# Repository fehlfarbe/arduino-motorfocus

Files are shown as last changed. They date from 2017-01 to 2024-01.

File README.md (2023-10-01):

# arduino-motorfocus

Simple moonlite focuser protocol implementation for Arduino and stepper motors.

Tested with Arduino Nano and cheap [28BYJ-48 stepper motor with driver](https://arduino-info.wikispaces.com/SmallSteppers) and [INDI / Ekos](http://indilib.org). Works also with [Pololu A4988 Stepper Motor Driver](https://www.pololu.com/product/1182) (see wiring).

Updated 3D/CAD models for TS 65/420 Quadruplet are available at Thingiverse: <https://www.thingiverse.com/thing:2063325>
Motor focuser for Starlight Feather Touch 2" by Cover1987: <https://www.thingiverse.com/thing:3593910>

## Installation

### Webupload via browser's Web Serial API

Only available for Chrome/Chromium at the moment. Visit <https://fehlfarbe.github.io/arduino-motorfocus>, connect your Arduino Nano and click the right button to upload the latest version :)

### Install via PlatformIO

1. Download and install [PlatformIO](https://platformio.org/install/ide?install=vscode)
2. Clone or download this project and unzip it
3. Open project with PlatformIO
4. Select the right config for your microcontroller e.g. `nanoatmega328` for Arduino Nano with 28BYJ-48 stepper, `promicro16` for Sparkfun Pro Mirco with 28BYJ-48 stepper or `nanoatmega328_A988driver` for Arduino Nano with A4988driver support in the bottom bar and upload to your Arduino (PlatformIO will download needed libraries automatically)

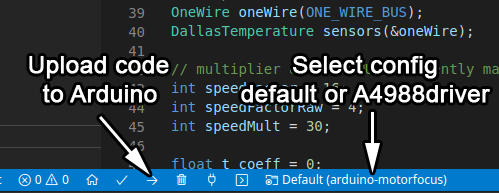
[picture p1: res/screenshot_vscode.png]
VSCode settings


## Wiring

### Wiring for 28BYJ-48 stepper motor with ULN2003A breakout board

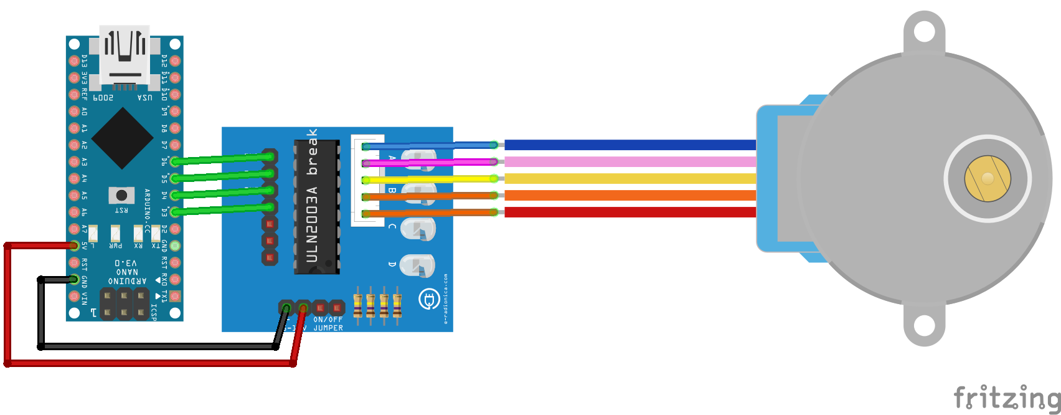
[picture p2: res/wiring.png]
28BYJ-48 wiring


### Wiring for A4988 driver

Select config `A4988driver` in VSCode bottom bar (step 4). You can change the microstep resolution (full step, half step, ...) with MS1, MS2, MS3 pins on the driver board. See more at [Pololu A4988 Stepper Motor Driver doc](https://www.pololu.com/product/1182) (Step (and microstep) size). If all pins are unconnected the driver will run in full step mode.
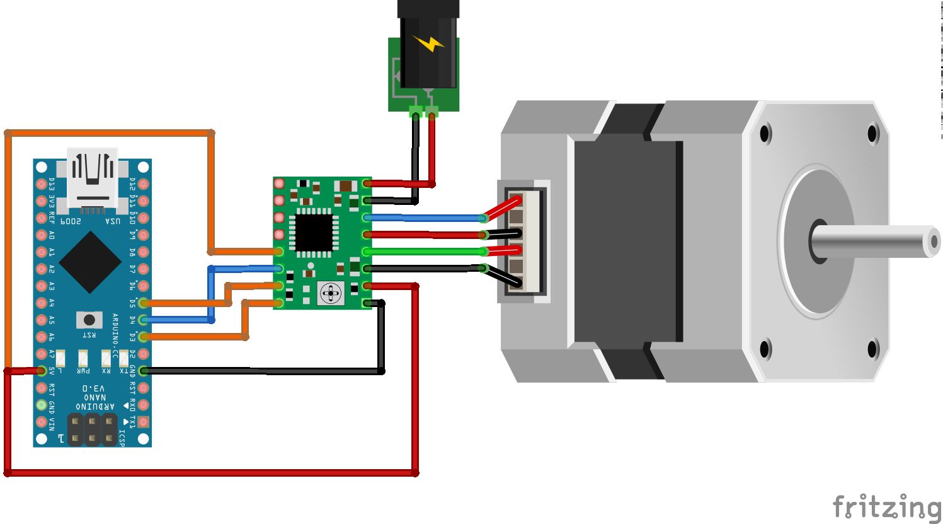
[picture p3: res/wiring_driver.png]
Stepper with driver wiring


### Wiring for in/out buttons

The internal pullups are active so you have to connect your buttons for manual focus to GND. The potentiometer is optional and can limit the maximum speed for manual focus.
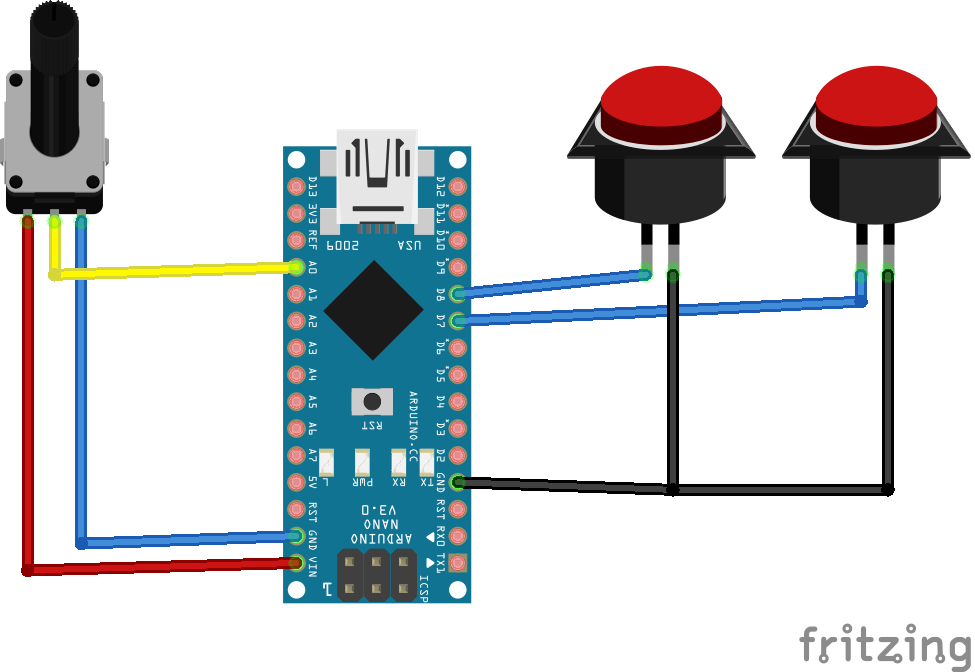
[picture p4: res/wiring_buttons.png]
Buttons wiring


### Wiring for temperature sensor DS18B20

You need a 4.7kΩ pullup resistor. If there is no sensor attached the temperatur will be zero.
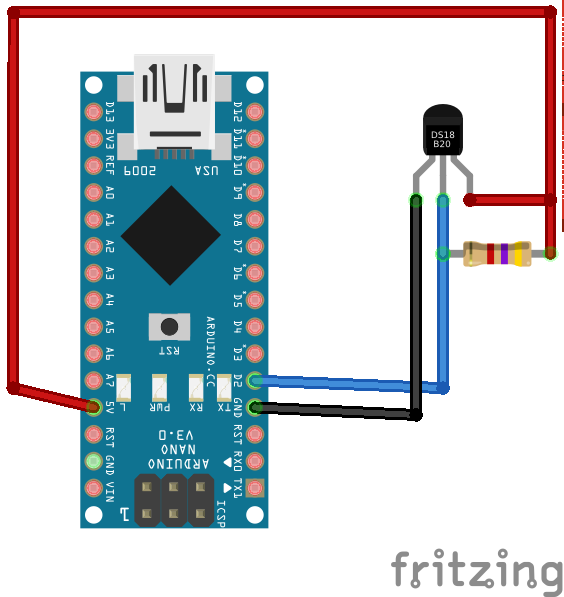
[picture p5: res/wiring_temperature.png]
DS18B20 wiring


## Troubleshooting

### ASCOM driver cant find the focuser

Some people reported problems with arduino-motorfocus and Windows/ASCOM. If you use the ASCOM-Moonlite.DRO.Focuser driver the focuser doesn't appear in the setup list.

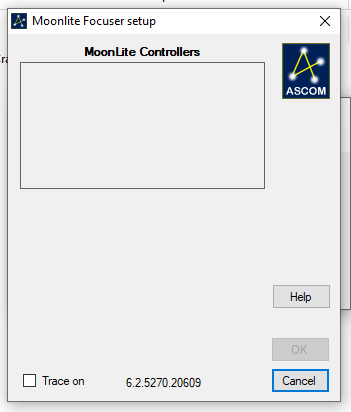
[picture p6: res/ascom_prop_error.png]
ASCOM driver cannot find focuser


This happens because the setup opens all COM ports, sends a command and waits for a proper response. Unfortunally Windows resets the device when the port is opened (DTR is set to low) and an Arduino clone needs a second or so to boot up so it won't receive the command and the setup gets a timeout. There are multiple ways to solve the problem:

1. You can flash the [MiniCore Bootloader](https://github.com/MCUdude/MiniCore) to your Arduino. This bootloader is faster and in my tests it was fast enough to get detected by the setup

2. Just install a 10µF or 33µF between RST and GND or remove the 100nF capacitor on the bottom of your Nano. You can see an image of the capacitor and further explanation on [this website](https://www.astroscopic.com/blog/disable-arduinos-auto-reset-connection)

3. Use a different Microcontroller like Arduino Pro Mini with an external USB-TTL converter and dont't connect the DTR line

And voilà the focuser will show up:

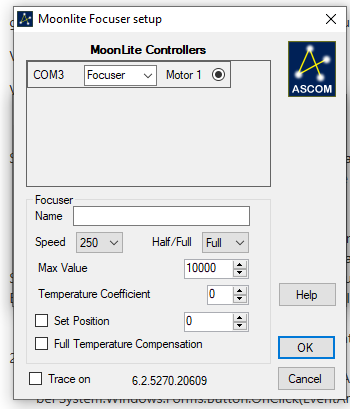
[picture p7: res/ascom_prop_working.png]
ASCOM setup finds focuser


### ASCOM driver finds the focuser but can't connect

Same problem as above. Unfortunally the first solution, flashing the bootloader, didn't work for me but the additional capacitor between RST and GND works.

### Other ASCOM errors

If there are different errors, please [open an issue](https://github.com/fehlfarbe/arduino-motorfocus/issues) and attach the logfile. You can activate logging for you focuser in the properties setup:

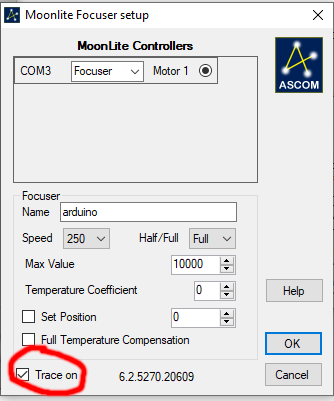
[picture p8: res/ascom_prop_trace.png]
ASCOM setup finds focuser


The logfile is located in `%HOMEPATH%\Documents\ASCOM`

You can also connect an USB-TTL converter to GPIO 10 to see all commands sent by your computer and some debug messages.

### The motor moves very slow

* Don't use a DEBUG build because SoftwareSerial printing slows down the microcontroller
* Check the full/half/... microstep setup of your driver
* Increase SPEED_MULTIPLICATOR and ACCELERATION in arduino-motorfocus.h

### The motor doesn't move

* Check wiring between microcontroller and your driver
* Check if manual focusing via buttons is working
* Check wiring between motor and driver, sometimes the motor coil cables are mixed up

## PCB

I made a simple PCB that connects all the parts and supports Pololu style driver boards and ULN2003A breakout board. The KiCAD project and gerber files are located at `hardware`.
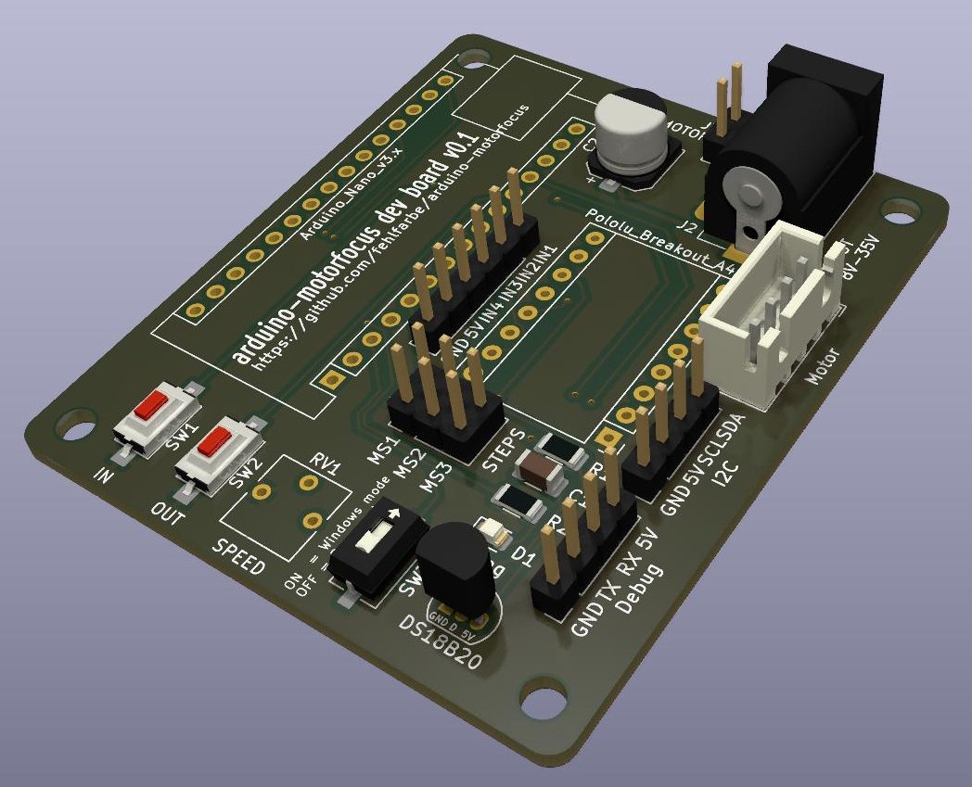
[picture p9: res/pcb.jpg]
PCB

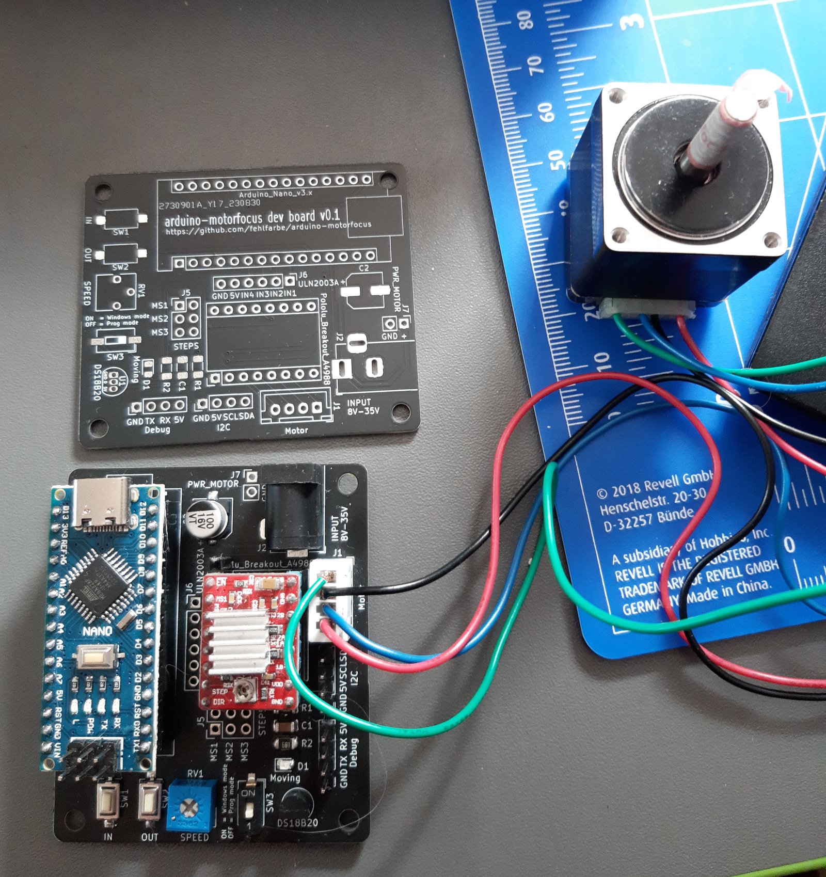
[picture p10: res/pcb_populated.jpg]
Populated PCB


## Arduino-motorfocus mounted on TS65/420 Quadruplet

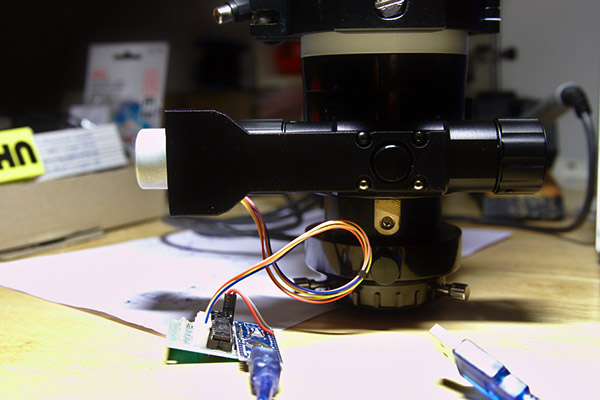
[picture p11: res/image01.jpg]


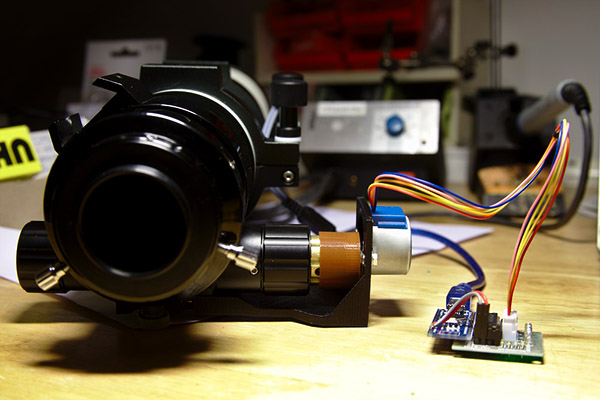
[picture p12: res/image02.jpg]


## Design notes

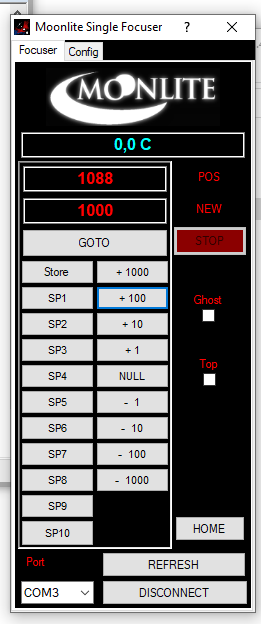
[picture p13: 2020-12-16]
res/standalone.png

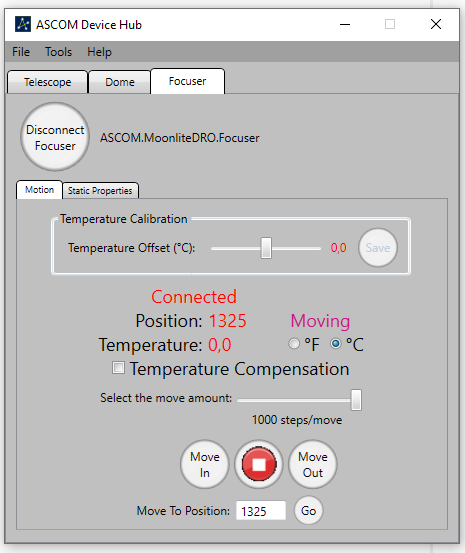
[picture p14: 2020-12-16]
res/ascom_working.png

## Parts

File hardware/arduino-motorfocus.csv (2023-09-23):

Source: | /home/kolbe/Arduino/arduino-motorfocus/hardware/arduino-motorfocus/arduino-motorfocus.kicad_sch
Date: | Sat 23 Sep 2023 21:14:49 CEST
Tool: | Eeschema 7.0.7-7.0.7~ubuntu22.04.1
Generator: | /usr/share/kicad/plugins/bom_csv_grouped_by_value.py
Component Count: | 23
Collated Components:
Item | Qty | Reference(s) | Value | LibPart | Footprint | Datasheet | DNP
1 | 1 | A1 | Arduino_Nano_v3.x | MCU_Module:Arduino_Nano_v3.x | Module:Arduino_Nano | http://www.mouser.com/pdfdocs/Gravitech_Arduino_Nano3_0.pdf
2 | 1 | A2 | Pololu_Breakout_A4988 | Driver_Motor:Pololu_Breakout_A4988 | Module:Pololu_Breakout-16_15.2x20.3mm | https://www.pololu.com/product/2980/pictures
3 | 1 | C1 | 10uF | Device:C | Capacitor_SMD:C_1206_3216Metric | ~
4 | 1 | C2 | 100uF | Device:C_Polarized | Capacitor_SMD:CP_Elec_6.3x5.9 | ~
5 | 1 | D1 | Moving | Device:LED | LED_SMD:LED_0805_2012Metric | ~
6 | 4 | H1, H2, H3, H4 | MountingHole | Mechanical:MountingHole | MountingHole:MountingHole_3.2mm_M3 | ~
7 | 1 | J1 | Motor | Connector:Conn_01x04_Pin | Connector_JST:JST_XH_B4B-XH-A_1x04_P2.50mm_Vertical | ~
8 | 1 | J2 | PWR_MOTOR | Connector:Barrel_Jack_Switch | Connector_BarrelJack:BarrelJack_Horizontal | https://de.aliexpress.com/item/1005002561919358.html
9 | 1 | J3 | Debug | Connector:Conn_01x04_Pin | Connector_PinHeader_2.54mm:PinHeader_1x04_P2.54mm_Vertical | ~
10 | 1 | J4 | I2C | Connector:Conn_01x04_Pin | Connector_PinHeader_2.54mm:PinHeader_1x04_P2.54mm_Vertical | ~
11 | 1 | J5 | STEPS | Connector_Generic:Conn_02x03_Odd_Even | Connector_PinHeader_2.54mm:PinHeader_2x03_P2.54mm_Vertical | ~
12 | 1 | J6 | ULN2003A | Connector:Conn_01x06_Pin | Connector_PinHeader_2.54mm:PinHeader_1x06_P2.54mm_Vertical | ~
13 | 1 | J7 | PWR_MOTOR | Connector:Conn_01x02_Pin | Connector_PinHeader_2.54mm:PinHeader_1x02_P2.54mm_Vertical | ~
14 | 1 | R1 | 10K | Device:R | Resistor_SMD:R_1206_3216Metric | ~
15 | 1 | R2 | 680 | Device:R | Resistor_SMD:R_1206_3216Metric | ~
16 | 1 | RV1 | SPEED | Device:R_Potentiometer | Potentiometer_THT:Potentiometer_Vishay_T73YP_Vertical | https://de.aliexpress.com/item/1005003399827077.html
17 | 1 | SW1 | IN | Switch:SW_Push | Button_Switch_SMD:SW_SPST_CK_RS282G05A3 | ~
18 | 1 | SW2 | OUT | Switch:SW_Push | Button_Switch_SMD:SW_SPST_CK_RS282G05A3 | ~
19 | 1 | SW3 | WIN | Switch:SW_DIP_x01 | Button_Switch_SMD:SW_DIP_SPSTx01_Slide_6.7x4.1mm_W6.73mm_P2.54mm_LowProfile_JPin | ~
20 | 1 | U1 | DS18B20 | Sensor_Temperature:DS18B20 | Package_TO_SOT_THT:TO-92_Inline | http://datasheets.maximintegrated.com/en/ds/DS18B20.pdf

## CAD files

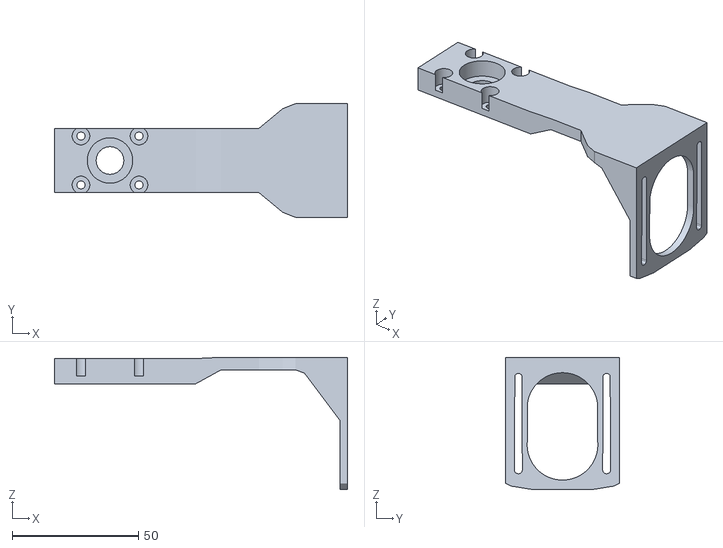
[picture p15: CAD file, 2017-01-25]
res/oaz_focuser_quadruplet_v3_04.STL
116.2 x 45.0 x 52.5

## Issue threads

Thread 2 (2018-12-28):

Buttons not worked for me, here is my solution.

franky384, 2018-12-28:
First of all, thank you for sharing your code,
but the push buttons never worked for me. So after some days of searching and trial and error i finally found a working solution.
Maybe you can have a look at it ?

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

[sketch_dec28a.html.pdf](https://github.com/fehlfarbe/arduino-motorfocus/files/2715402/sketch_dec28a.html.pdf)

franky384, 2018-12-28:
I have tried it like in that example, but it hadn't worked for me. I can try it again with my changed code.

fehlfarbe, 2019-02-17:
Should be fixed now. I activated the pullup resistors for button input and checked for BUTTON == LOW. So the wiring in your first post is correct.

Closed 2020-12-21.

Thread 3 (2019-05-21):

AccelStepper.h: No such file or directory

AndiPhotonen, 2019-05-21:
Hi,
First of all I'd like to thank you for realizing this nice project.
I downloaded the Project as a zip and extracted it to my Arduino folder.
But when I try to compile it, I get the error that it can't find the AccelStepper.h
Did I miss something or do you have a tip for me?
Thanks!

fehlfarbe, 2019-05-21:
Hey Andi,
the Accellstepper library is missing. You can install the library with Arduino Studios library manager: https://www.arduino.cc/en/Guide/Libraries just search for accelstepper, install the current version and recompile.

AndiPhotonen, 2019-05-22:
Thank you! now it works fine

Closed 2019-05-22.

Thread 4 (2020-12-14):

Not anymore compatible to Moonlight SW

energiebrand, 2020-12-14:
Hi,
Build the controller using an Arduino NANO clone (FTDI chip), ULN2003 stepper druver and the gear stepper motor. The sketch works out of the box when using the manual control via the buttons.

Just for fun I tried to use the original Moonlight non-ASCOM controller SW but unfortunately it only connects, read the temperature and actual step value and does nothing. The Moonlight SW hangs up (WIN 10 and WIN7). When connecting via PUTTY serial, everything works fine. All listed commands are working.

Then tried the Moonlight ASCOM driver. The driver is recognized by CCDCiel SW for example. Then I open an ALPACA driver and this opened the Moonlight ASCOM driver. But this ASCOM driver does not recognize the Adrduino (sketch).

So I think maybe Moonlight changed something in their SW (Non-ASCOM controller App as well as Ascom driver) so that your sketch is non more supported. Could that be? Did you try to to connect with the latest Moonlight SW?
Best regards and however thanks for the Sketch!

fehlfarbe, 2020-12-14:
Hi,

to be honest I tested the setup only with the INDI moonlite driver. But many people asked in the last weeks if it will run on Windows with ASCOM. So I set up a Win10 VM and tested the "Moonlite Single Focuser" which worked like expected (just with my nano and the motor on a breadboard)

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

Then I tried the Moonlite DRO ASCOM driver but it can't even find the COM port:
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
Seems like the driver opens all COM ports, sends a command and waits for the right response. Unfortunately the Arduino Nano resets when the COM port is opened and it takes 200ms or so before it's ready to receive commands which takes too long for the Moonlite driver.
You can turn off the auto reset with a 10nF capacitor between RST and GND (I tried a 47nF which is also working).
Then open the properties windows again and the Arduino will show up. If not, close the windows, press the RESET button on the Nano and try again. It worked on the second try with my setup.
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

Let me know if it's working, so I can update the readme :smiley:

energiebrand, 2020-12-15:
Hi and thanks a lot for fast response!

The solution with capacitor / Reset seems to be the right way but I have only partly success.
Firstly after connecting a 33nF C the Arduino connects with the Dual Focuser Moonlight SW and I was able to control the motor as expected. Very good!

Then I connected via ASCOM using the Moonlight focuser driver and CCDCiel SW. Now it found the Arduino as a Focuser. Very good!

Then I checked with the Single Focuser Moonlight SW on a WIn7 PC but no success...

Then went back to the WIN10 PC and tried again with the Dual Focuser Moonlight SW...no success anymore!!! I tried with several C´s (15nF, 33nF, 22nF, 1mF, new boot of the PC, Reset manually of the Arduino, no chance anymore. The Arduino always connects in the first or second attempt, send some data (Pos and temperature) and then disconnects. Tried it dozend of times.

After that back to the ASCOM driver and always success. I removed the USB, no focuser, reconnceted the USB and success with the ASCOM driver.

So no luck anymore with the non-ASCOM driver. (I cannot use the Single driver because I deleted the SW in a not correct way and it seems that somewhere parts are remaining. This results in that I cannot anymore install the single focus driver...)

To summerize:
- with Moonlight ASCOM driver working on a WIN10 installation using a 15nF, 33nF, 22nF, 1microF
- unfortunately I cannot do more things with CCDCiel because I do not have a camera, but I can see that there is a communication between the Arduino and the PC (RX and TX LED flashing)
- no permanent connection anymore with Dual focuser SW, just a short data exchange
- also it is not possible to open the ASCOm device hub, but maybe I am doing wrong or anything more is needed

So what to do? Since currently I am only using the "Manual button" function I can live with that.
Also later on when I will go to astrophotographie the ASCOM driver works.
Only limitation for me is the non-Ascom SW.

However the capacitor is working and helps. The other problems seems to be a problem of the used PC and the Arduino clone version.

So no problem with your sketch and I think you should close this issue but add some information. I would recommend to add the C in the description and schematic!

Thanks a lot and if you have any further idea you are welcome!

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

energiebrand, 2020-12-15:
Tried the whole day to get more about the problems I have...

Maybe a 1microF is a better solution. I noticed that the ASCOM driver always recognized the Arduino when the USB cable was connected (...and did not recognize when USB was open), but in many cases there was no communication between the Arduino and the ASCOM driver after the connection was established. So I changed to a 1microF C and RX/TX is flashing constantly.
So that means even if the ASCOM driver windows shows that is has found a COM port and a focuser is detected there could be that there is no communication.

In addition meanwhile I got the Single Focuser Moonlight SW running again but same problem as I had without the C. It connects now stable, sends some information (Temp and Pos.) and after that it freezes...

fehlfarbe, 2020-12-17:
Sorry my bad, I used a 47**µ**F capacitor. I also found different hints/solutions:
- Update the bootloader: the Arduino clones from China have the old bootloader that takes 1-2s too boot up. I flashed the newer Optiboot with [MiniCore](https://github.com/MCUdude/MiniCore) that boots much faster. At least the setup finds the focuser without the capacitor. But I still can't connect with ASCOM Device Hub.
- Remove the 100nF capacitor on the bottom as described here: https://www.astroscopic.com/blog/disable-arduinos-auto-reset-connection. After that you have manually press the reset button if you want to upload a new firmware
- Does it also freeze if you don't connect the temperature sensor? I just wired the motor but no sensor. Maybe the Arduino sends some bad numbers and the driver freezes?
- Sometimes I have to press the "connect" button twice on the SingleFocuser but after that it is stable
- The DualFocuser looses the connection after some seconds. I assume that happens because it sends an unknown command (starting with a number), doesn't get a proper answer and runs into a timeout:
  ```
  [01:01:21:086] Got new command: GT␍␊
  [01:01:21:108] GT:␍␊
  [01:01:21:114] GT␍␊
  [01:01:21:213] temperature: -127.00␍␊
  [01:01:21:267] Got new command: GP␍␊
  [01:01:21:290] GP:␍␊
  [01:01:21:296] GP␍␊
  [01:01:21:301] current motor position: 0x0820 = 2080␍␊
  [01:01:21:345] Got new command: 2GP␍␊
  [01:01:21:365] 2G:P␍␊
  [01:01:21:372] 2GP␍␊
  ```
  I just updated the code so it will ignore the leading "2" and just parses the command. So motor1 and motor2 show the same values. After that the DualFocsuer doesnt disconnect but freezes :laughing: but SingleFocuser still runs fine.

energiebrand, 2020-12-17:
Thanks  a lot for the deep-dive into the problem!
Yes I have seen in an other discussion that someone has used a much bigger C and thats why I tested also with 22 and 47microF. However a 1microF does also the job and connects stable to the Single Manual Focuser SW.

And yes my NANO clone have the old bootloader.

I do not use the temperature sensor, so the pin is open in all my tries. It shows 0° but still freezes with the Single Manual Focuser SW after a first and short data transfer. It changes the display from "No data" to "0" and the temperature to 0°.
I had only one attempt 3 days ago where it works and it was possible to control the motor 100% and I think this was by random.

Using the Dual Focuser SW: the Arduino connects also, shows the 0 values on both rows but than disconnects after 5 seconds like yours, but without your sketch modification!

Now the bad thing for you... :-(  yesterday I completed my installation and closed the cover. As I said currently I will use the focuser just manually with the buttons in a hand-box I am printing at this moment.
So with this installation I will not going on to flash a new bootloader. However it would be very interesting to continue and see the results. Unfortunately at the moment I don't have another NANO for more testing.

But it could be that when changing to astrophotography I will use your solution again and need a SW a (ASCOM) controlled focuser. Then I will come back to your proposals.

But regarding the ASCOM driver. Like you my NANO will not really run with it. It connects and most time I see a continously data transfer (RX/TX LED flashing) but no chance to control the motor. Maybe it is the missing astro camera maybe it will not work anyway.

So from my side I will stop here with the current installation but will answer here if I got new results with another NANO I will buy in the future. Thanks a lot for your works! Well I think think discussion will help other people if they are running into similar problems. Attached some pictures of my Newton and the focuser. :-)

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

fehlfarbe, 2020-12-21:
Nice prints! I added your Thingiverse CAD models to the readme :smiley:

If you want to do further investigations you can enable trace/logging in ASCOM and maybe find an error in the logfile and connect a serial/ttl converter to GPIO 10 and see your Nano's debug output (https://github.com/fehlfarbe/arduino-motorfocus#other-ascom-errors)

I will close the issue for now but feel free to reopen :)

Closed 2020-12-21.

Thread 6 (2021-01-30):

may be a bug...

sergio49, 2021-01-30:
Hi, I think you have a mistake in your hexStrToLong converter preventing speed change to work.

at line 329 I think it should be  :
line.toCharArray(buf, line.length()+1);    (+1 missing)

if you change this you have to delete *16 on current and target positions. Then speed change and positionning works fine in ekos.
I've just tested it.
Thanks for your work I use it on my 80ED too :)

fehlfarbe, 2021-02-02:
Thanks for bugfixing and testing :)
I merged your changes to master

energiebrand, 2021-02-08:
Hi all
thanks for BugFixing!
Used the focuser only manually with a modified sketch (added a switch for fast movement) so far.
Now I´m running the focuser with ASTROBERRY: KStars / EKOS / INDI with the latest modifications and can confirm that it is working!

Closed 2021-12-01.

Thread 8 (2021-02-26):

Motor does not run in script

19dexter86, 2021-02-26:
Hi, the motor turns with the buttons without any problems.
But it does not work via the Moonlight. Temperature is displayed. here is an snippet from the logfile.

[ASCOM.MoonLite.1733.440170 - Kopie.zip](https://github.com/fehlfarbe/arduino-motorfocus/files/6051056/ASCOM.MoonLite.1733.440170.-.Kopie.zip)

19dexter86, 2021-02-26:
problem solved. had to move ist one time with buttons, then it works with sgp

Closed 2021-02-26.

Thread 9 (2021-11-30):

DS18B20 wrong wiring

energiebrand, 2021-11-30:
Hi Marcus,
build your motor-focusser last year and still in operation with Astroberry / INDI on my Newton. We had some discussion about the problem with ASCOM...
Now I developed some new 3D parts for a SVBony APO since the buttons on the 1:10 gear are bigger than yours.
However first time I added an 18B20 and burned my fingers... the wiring on your diagram is wrong. + and - are inverted.

fehlfarbe, 2021-12-01:
You are right! I think the DS18B20 part in Fritzing is wrong because it says VDD | DATA | GND:

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

But data sheet says it's GND | DATA | VDD https://datasheets.maximintegrated.com/en/ds/DS18B20.pdf

The broken Fritzing part might be the reason why I burned my fingers several times on the temperature sensor too :laughing:

Closed 2021-12-01.

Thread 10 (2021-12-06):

stepper not disabled in fringe condition

jvanderk, 2021-12-06:
In the code

    isRunning = false;
    if (millis() - millisLastMove > millisDisableDelay)
    {
      // Save current location in EEPROM
      if (lastSavedPosition != currentPosition)
      {
        EEPROM.put(0, currentPosition);
        lastSavedPosition = currentPosition;
        debugSerial.println("Save last position to EEPROM");
        stepper.disableOutputs();
        debugSerial.println("Disabled output pins");
      }
    }

the stepper is not disabled if the lastSavedPosition is identical to currentPosition. I ran into this when testing, it is unlikely to occur in real life.

A simple solution may be to pull the disableOutputs() line out of the if command.

fehlfarbe, 2021-12-07:
You're right, thanks! :)

Closed 2021-12-07.

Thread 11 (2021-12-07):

Several updates to enable use on Sparkfun Pro Micro

jvanderk, 2021-12-07:
Trying to use the code on a Sparkfun Pro Micro clone, I ran into several issues:

1. serialEvent was not called automatically after loop().
2. SoftwareSerial had a compilation issue related to the assembly in there.
3. An issue with temperature string formatting.

Made changes to code and added some documentation and a choice to platformio.ini

I'm going to try to submit the changes using a pull request but I've never done that so bear with me....

jvanderk, 2021-12-07:
I think I created a pull request but not sure how to link that to this issue.

fehlfarbe, 2021-12-07:
Thanks! I will take a look at it tomorrow :)

fehlfarbe, 2021-12-08:
I think I can't push my changes on your pull request but I created a new branch `promicro` with your changes and added some new environments for different configs to platformio.ini. There is a patched version of SoftwareSerial on Github, so I'm using this repo for SoftwareSerial so other users don't have to modify the lib.

Can you take a look at it?

jvanderk, 2021-12-08:
Cool!

Tested

```
# Sparkfun ProMicro
[env:promicro16]
[env:promicro16_debug]
```

environments and both seem to work (manual buttons and ekos controlled).

Patched version of SoftwareSerial is OK.

Still in a maze on the pull request workflow :--)

Closed 2023-06-08.

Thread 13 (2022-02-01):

I'm stuck at Arduino flash

zeltragh, 2022-02-01:
Hello,

I try to flash my arduino nano with the arduino-motofocus project but error comes.

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

i don't know i did bad...

Can you help me ?

zeltragh, 2022-02-01:
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

fehlfarbe, 2022-02-01:
Hi!

Open a terminal in VSCode and type

`pio platform install atmelavr`

This should install the needed platform. If this doesn't work, please add a screenshot or log output here :)

zeltragh, 2022-02-06:
Thank you for help.
Finally it was pio platform issue. After reinstall of this , problem solved.

Closed 2022-02-06.

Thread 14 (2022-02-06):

Indi driver and no response on Ekos interface.

zeltragh, 2022-02-06:
The focuser is ok an Ascom environement.
But in INDI (with Ekos) no communication with arduino.
I try all baud rate and no result.
Log file didn't help:

"zeltragh@Stargate:~/.indi/logs/2022-02-06/indi_duino$ cat indi_duino_12\:56\:12.log
INFO	-2834.245937 sec	: Session log file /home/zeltragh/.indi/logs/2022-02-06/indi_duino/indi_duino_12:56:12.log
INFO	-2651.273809 sec	: Scan complete. Found 2 port(s).
"

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

Maybe the choose of driver ? Wat is the compatible driver in INDI ? arduino focuser, moonlite , moonlite DRO ?

zeltragh, 2022-02-06:
OK i found it. Moonlite on 9600 baud.

Closed 2022-02-06.

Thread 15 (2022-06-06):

Random movements

PdP03, 2022-06-06:
when I power the motor up (5v Arduino), it starts to move, then when i connect it to ekos or moonlite single focuser and I gave a goto (ex: 10000 steps) it goes where it has to go, but after 10 second it starts again spinning. I have tried to change everything, but nothing seem to have any affect, may be a bug in the code?

fehlfarbe, 2022-06-06:
Hmm sounds a bit like wrong wiring or interference :thinking:

Can you try the examples from the AccelStepper library? Maybe some example with longer pauses between moving commands to check if it's wiring related or a bug in the code.

If AccelStepper examples are working:
* Does the motor always move in the same direction with the motofocus code?
* Are the buttons connected? Maybe there is a broken button?

cybye, 2022-06-10:
got the same problems right now on esp8266 D1 mini. the sketch is moving the motor - one direction - probably endlessly and N.I.N.A. // ascom is patiently waiting in initialization(did not debug yet, was there any reason for movement on initialization in the code?).  btw. aside the capacitator, it looks like keeping the RST pin supplied from 5V/3.3V with a <1k resistor is an alternative. had no capacitator at hand.

cybye, 2022-06-10:
(early) success with defining the 'unconnected buttons as HIGH. might be a board thing

```
   int btn_in = HIGH; // digitalRead(BTN_IN);
   int btn_out = HIGH; // digitalRead(BTN_OUT);

```

PdP03, 2022-06-12:
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

I don't use buttons. One thing I forgot to mention is that if I upload the code, disconnect the Arduino and reconnect it starts spinning. When I stop it through software (Moonlite Single Focuser, tried with Ekos, same result) it slows down but whatever the direction where it was spinning, it starts going up with the number of steps. This happens both with an Arduino Uno and a nano. I even tried to change the motor and the driver with no results.

cybye, 2022-06-12:
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

could you try locating these two lines in the sketch
```
   int btn_in = digitalRead(BTN_IN);
   int btn_out = digitalRead(BTN_OUT);
```

and replace them with

...
   int btn_in = HIGH; // digitalRead(BTN_IN);
   int btn_out = HIGH; // digitalRead(BTN_OUT);
...

?

PdP03, 2022-06-12:
Don't know why, but it seems to work. Tomorrow I'll do some other tests, I'll let you know if everything checks out.

fehlfarbe, 2022-06-12:
Hey,

sorry, I don't have much time at the moment. It sounds like the Button input Pins are floating so they get some random signals.

The pinMode setup should prevent this already with activating the internal PULLUP resistor so the input should always be HIGH if nothing is connected (or the button is open)

```
  pinMode(BTN_IN, INPUT_PULLUP);
  pinMode(BTN_OUT, INPUT_PULLUP);
```
https://github.com/fehlfarbe/arduino-motorfocus/blob/master/src/arduino-motorfocus.cpp#L101

But maybe there is a problem with some boards or so. If you don't need the buttons you can just change the code like @cybye suggested or you can add external pullup resistors. Just add a 10K resistor between BTN_IN and 5V (or 3.3V for ESP8266) and do the same for BTN_OUT and 5V/3.3V.

Maybe I will find some time for further investigations this week.

PdP03, 2022-06-13:
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

With this fix, everything works fine, thanks a lot man!

Closed 2022-06-13.

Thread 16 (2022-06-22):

Focuser is initializing in moving motor state on connection

cinosh07, 2022-06-22:
I'm using 28BYJ-48 stepper motor with ULN2003A breakout board and when I connect to the focuser, It always start in moving state to true. I have to go in the device hub, make a small move, then the moving state change to stop

Here is my log
[ASCOM.MoonLite.txt](https://github.com/fehlfarbe/arduino-motorfocus/files/8959026/ASCOM.MoonLite.txt)

cybye, 2022-10-03:
#15 <- please check if this helps

cinosh07, 2022-10-03:
> #15 <- please check if this helps

Thanks for your reply, That's the first thing I've tried. At first I was thinking that it was doing that on only 1 of my 2 focuser. But finally it does it on both. On with 5v motor and the other one with the A4388 driver and 12 volt. Both does the same thing. But I didn't change the bootloader. That the original with capacitor.

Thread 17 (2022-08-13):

wrong wiring for A4988 ?

Holgervisitinggithub, 2022-08-13:
Disclaimer: I am no expert at all, but at least it worked for me.

Picture of the wiring from A4988 to the arduino seems to be wrong.
The "DIR" pin from A4988 needs to be connected with D3 instead of D5
The "Step" pin needs to be connected with D5 instead of D6

according to the code
#define PIN_DRIVER_DIR 3
#define PIN_DRIVER_STEP 5

Thank you for the great work!
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
!

Ardufan, 2022-08-18:
I noticed as well that the wiring and code are inconsistent.

And I would recommend to take the chance to rename this piece of code:

#define PIN_DRIVER_ENABLE 4

The pin n. 4 (arduino side) is connected to the SLEEP and not the ENABLE pin on the driver side. It would be advisable for code clarity to rename this #define as :

#define PIN_DRIVER_SLEEP 4

and change accordingly this line in setup():

stepper.setEnablePin(PIN_DRIVER_ENABLE);

to

stepper.setEnablePin(PIN_DRIVER_SLEEP);

fehlfarbe, 2022-08-22:
Hey thanks! I updated the picture and changed the name to `PIN_DRIVER_SLEEP` :+1: (You may have to clear your cache to see the updated image)

Ardufan, 2022-08-22:
thank you for sharing your nice code!

PS: I added to my own copy a TM1637 6 digit display, just to show the current position also when operations are manual.
It only requires 2 arduino DIO pins and the library TM1637TinyDisplay6

Closed 2022-08-22.

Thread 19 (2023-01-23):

Ideas for working around "avrdude: butterfly_recv(): programmer is not responding" ?

frankbraker, 2023-01-23:
When I try to upload the hex file (regardless of which target I select), I get something along the lines of:

Found programmer: Id = "F"; type = @
    Software Version = \xdc.u; Hardware Version = \x93.\xf0
avrdude: butterfly_recv(): programmer is not responding
avrdude: butterfly_recv(): programmer is not responding
avrdude: error: buffered memory access not supported. Maybe it isn't
a butterfly/AVR109 but a AVR910 device?
avrdude: initialization failed, rc=-1

It always fails.

I've confirmed my hardware is based on ATMEL M328P.  It's a nano.

I've also gotten the same result for more than piece of hardware and multiple cables, and with anti-virus disabled in Windows.

This nano loads the basic examples fine from the Arduino IDE.

Toboi, 2023-02-01:
I am not sure if this is the same problem I experienced, the output is different.
But there seems to be a version of the Arduino nano with a new bootloader which requires a different board variable (See [platformio docu](https://docs.platformio.org/en/stable/boards/atmelavr/nanoatmega328new.html))

In the platformio.ini I had to change
```
# Arduino Nano
[env:nanoatmega328]
board = nanoatmega328
```

to
```
# Arduino Nano
[env:nanoatmega328]
board = nanoatmega328new
```

fehlfarbe, 2023-02-01:
Good idea @Toboi !

The nano has different bootloader versions that aren't compatible so maybe replacing the board will fix it.

If this doesn't work you could try to upload the compiled hex file manually via terminal: Activate verbose output in the Arduino IDE and upload a sketch. Look for the `avrdude` command that is used to upload the hex file in the output window of the IDE and run the same command with the replaced path for the hex file (should be at `arduino-motorfocus/.pio/build/nanoatmega328/firmware.hex`)

frankbraker, 2023-02-04:
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

This worked for me!!  Thanks!!

Closed 2023-02-04.

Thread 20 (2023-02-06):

Do the buttons work for you?

frankbraker, 2023-02-06:
I was certain there was something wrong with my hardware - after trying several times with one I had wirewrapped, and finally using a breadboard and it still seemed like it was dead... and then when the house was as quiet as it could get in the middle of the night, I finally noticed a very very quiet bumping sound coming out of the stepper motor when I pressed the buttons.

I tried changing the # of steps in BTP_STEP from 32 to 4096 and that helped - but the whole thing is still way too slow, I can't see the knob moving at all.

Am I still doing something wrong?  Do the buttons work for you?

I would file this under "tips and tricks for troubleshooting" - and just getting it to make a sound or see it moving seems like a good first step.

fehlfarbe, 2023-02-06:
Do you use the 28BYJ-48 stepper motor with ULN2003A breakout board or a different driver like the A4988?

The ULN2003A breakout board works for me out of the box with a passable speed:

https://user-images.githubusercontent.com/3355380/217092530-a81abef7-8d06-46c4-a3c4-9a8a5a7ba983.mp4

frankbraker, 2023-02-07:
I'm using the 4988 (shown at the bottom of your breadboard).  Because I'm using this with a Moonlite focuser, I think the stepper motor on the focuser is geared way down to go pretty slow even when it's full stepping.  I imagine I'll want it to go as fast as it possibly can when using the buttons, and only when using the ASCOM driver for fine control it might be more appropriate to go slower then (albeit, probably not necessary to go slower).

fehlfarbe, 2023-02-07:
Just to be sure: I tried with the A4988 driver and a random stepper motor. The steps/speed is quite fast/ok.

https://user-images.githubusercontent.com/3355380/217333119-50e2b766-fd25-47c9-8771-9daf9c98cf68.mp4

So I think it's the reduction gearbox. Maybe it helps when you increase BTP_STEP and speedMult (that limits the maximum speed for movements)
https://github.com/fehlfarbe/arduino-motorfocus/blob/4e0ffb6a2911d06b1b8edb75302927f77b042a93/src/arduino-motorfocus.cpp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
and increase the acceleration rate:
https://github.com/fehlfarbe/arduino-motorfocus/blob/4e0ffb6a2911d06b1b8edb75302927f77b042a93/src/arduino-motorfocus.cpp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

frankbraker, 2023-03-13:
This issue can be closed as far as I'm concerned.

Thanks so much for all the help!  Sorry I didn't get back sooner, but I've been away.

I was finally able to get mine working properly.  The labels on the A4988 confused me, where 1A, 1B, 2B, 2A should be paired as 1A with 2A and 1B with 2B.  But that's not all - because I'm using a Moonlite stepper motor it's a unipolar, which means don't connect the 12V line (only connect the 1+, 1-, 2+ and 2- lines).  See page 8 of http://www.indilib.org/media/kunena/attachments/1/HighResSteppermotor107.pdf and OP of this thread https://www.indilib.org/forum/general/1260-controlling-moonlite-focuser-from-raspberry-pi.html for details.

After working through these I finally have things moving, and I set the current limiting Vref to 0.24v to facilitate the 0.15A the motor can handle, using S1=0.2 (source http://hiletgo.com/ProductDetail/1952643.html ).  R10=20,000, so Vref(target current) = 0.15A * (8* 0.2) = 0.24V  -- see https://www.instructables.com/Drive-a-Stepper-Motor-with-an-Arduino-and-a-A4988-/ and notice that any "0.8" magic number is really 8*S1.  Hopefully this helps someone.

This still didn't work well with whole steps (missed a lot of steps even with BTN_STEP=32 - but works okay with 1/8 stepping or even 1/4 stepping.

Closed 2023-03-13.

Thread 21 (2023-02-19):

Nema17 with A4988

HansBeg, 2023-02-19:
Hallo and many thanks to share this work with us. After 35 years without electronic bricolage you invited me to follow you. Thanks! I have Win10, the Nano and the 28BYJ-48 stepper motor with ULN2003A breakout board, with the temperature sensor wired. With the buttons it works out of the box. The „nanoatmega328new“-issue I found out by myself by hazard.
But, I have two issues/ problems.

At first „ASCOM cant find the focuser“:
After using an 0,1µF capacitor I got the connection! I tried also the way with „MiniCore Bootloader“. I used the master „Nano as ISP“. Than I choose ATmega328 offered by MiniCore (in Sketchbook), see Pic. But „Burn Bootloader“ doesn’t happen. When I select the Arduino Nano board I burned the bootloader. And now I can  reach the setup, and then? How can I operate with the Focuser (hardware)? Moonlite Single Focus find the focuser, set the temperature every 0.5sec, but no movement is possible. I found an other Application: AP Mini 19.12-1. This works fine with temperature – but as non ASCOM device, as a simple MoonLite. When I choose „ascom“ the motor never stops. I can live with AP Mini, this is ok for me.

At second: I need the bigger motor, an Nema 17 with the A4988 driver. I made the wiring on the breadboard, using MB102. I checked out before using, that the 12V goes to the + and – rails. The 5V I got via USB. Than I wired, switched „on“, the yellow light blinked  few times and the voltage converter for 5V said good bye. The motor doesn’t moved - I know the motor need too much current for the MB102. I checked the data sheet which Az-Delivery offers. I found:

„Connect RST pin to the SLEEP pin to keep the driver enabled (Black wire).
REMEMBER to put a large 100μF decoupling electrolytic capacitor across motor
power supply pins, as close to the board as possible, like on connection diagram“

But in the wiring diagram of the project I didn’t find such need. And what is with the connection between RST and Sleep? Did you tested the combination A4988 with a Nema motor? Is the wiring in the project right?  (I read the closed request #17)

regards Hans

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

fehlfarbe, 2023-02-22:
Hi Hans,

I will try to take a deeper look into your problems this week.

Just for now:

I tested a Nema motor with A4988 driver some weeks ago -> https://github.com/fehlfarbe/arduino-motorfocus/issues/20#issuecomment-1421269295
I connected the 12V of my bench power supply directly to the A4988 driver. Did you connect the 12V to MB102 and the 5V output of the MB102 to the driver? I think the motor draws too much current for the small 12V -> 5V linear converters of the MB102 so just connect the 12V directly to the driver VMOT / GND as suggested here **and check that you don't mix it up with the 5V / VDD pins**! You can also add the 100µF to the motor power supply lines. I didn't need them for my testes but if the motor has some load they might be required.
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
https://www.pololu.com/product/1182

HansBeg, 2023-02-22:
Hi,
yes, the burned MB102 was my fault. Learn by errors.
I loaded the actually code - without success. Then I added in line40 also the "new" and the Nano flashed (without an capacitor btw GND and RST. The Nema 17 (with Elko) turns with the buttons and with AP Mini after the second try.  Uff!
The motor works loud and hard. I will use microsteps. On the A4988 are the MS1, 2 and 3. In the data sheet I see this.

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

Does it means High: 5V and Low: GND? Or should I set D9 and D10 and connect?

kind regards to Dresden, my favorite town since years.
Hans

fehlfarbe, 2023-02-26:
Hi,

so it's working now? Does the motor rotate or does it just "vibrate"? You can change the maximum current with the small potentiometer on the driver. Maybe it doesn't get enough current?!

Indeed, LOW means connected to GND and HIGH means connected to 5V. The pins have internal pulldown resistors so if they are unconnected they are pulled down to GND.

And don't forget to connect RST to 5V and SLEEP  to D4. The Nano sets the sleep pin after some seconds to disable the driver and save energy and disables sleep when a move command or button press was detected. If you don't want/need this behavior you can connect RST to SLEEP and D4 stays disconnected.

D9 and D10 are only pins for debug reasons. You can connect a USB-TTL device to get the debug messages printed by "debugSerial.print()" functions. Just leave them unconnected.

I'm checking the Arduino firmware with some programs on Windows and found some little bugs that I'm fixing at the moment. Where did you download the "AP Focus MoonLite" program?

Best regards from Dresden,
Marcus

HansBeg, 2023-02-27:
Thank's for the answer. The motor turns, but not smooth. Since a few steps it is a pause. But, when I say 10 turns (in AP Focus) I get 10 turns. In the web is this behavior described.
The microsteps are now ok.
The download page I hadn't noticed. But I found it. Here you are: https://miltonhill.us/software/index.html
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
Meanwhile I tried out the Moonlite ascom (Build: 1.3.1.0) with little success. I can read the temperature. After reset of the nano the motor fliged (zappelt) but  I can't do anything to turn some steps.
many regards from Reutlingen

HansBeg, 2023-02-27:
P.S.: sometimes (after 1min or so) happens one given funktion, e.g. "HOME"
The whole time TX and RX are blinking. Temperature is always up to date (change after 1 or 2 secs when neccessary)
Hans

fehlfarbe, 2023-02-27:
Thanks for the feedback. I updated the code and tested with APT (Astro Photography Tool) and the AP Mini tool and they worked for me. You dont' have to modify the config again. I added the `nanoatmega328new_A4988driver` config that you can change on the bottom of VSCode:

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

HansBeg, 2023-03-01:
Hallo and many thanks for your labor. I updated my software. I works. I realized, that only full steps and 1/4 steps are possible. I don't know why. But that's good and enough for me. Now I have to fill this in a appropriate box, respectively on a conductor plate.
I wish you the very best for the future!
Bye

fehlfarbe, 2023-03-03:
Nice! Feel free to open a new issue if there any problems :smile:

Closed 2023-03-01.

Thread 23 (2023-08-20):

Upon connecting, the red light blinks 100011000 at about 0.5Hz until I disconnect

frankbraker, 2023-08-20:
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

When I connect from N.I.N.A, Windows claims it connected, but the red LED on Arduino blinks 1 on, off for about a second, then 2 rapid ons, and off for about another second.

[ASCOM.MoonLite.2015.119360.txt](https://github.com/fehlfarbe/arduino-motorfocus/files/12387055/ASCOM.MoonLite.2015.119360.txt)

I tried it again with different cables, and maybe the LED is just blinking on and off at about 1Hz.  I might be mistaken about that double blink in the pattern.

fehlfarbe, 2023-08-28:
Hey, sorry for my late response. The builtin LED turns on when the motor is moving but it seems that the target position and the current position is the same in your screenshot even though "is moving" is set to true :thinking:

The connection seems to be ok because NINA sends commands and gets responses but you can't move the motor with the buttons?

frankbraker, 2023-08-28:
Correct, both the buttons are unresponsive, and there is nothing that can be done via the driver in NINA.

fehlfarbe, 2023-08-29:
Might be a bug for the GI ("is motor running?") command. Can you try this branch: https://github.com/fehlfarbe/arduino-motorfocus/tree/fixrunning ?
I tested it with NINA in my Windows VM and it seems to work.

Also the LED should only turn on when the motor is moving.

frankbraker, 2023-08-30:
Well there are 2 lights: the amber one lights up (but fails to move) when I press a button.  It's the red light that is doing the blinky pattern.

I'll try the branch and let you know if it behaves differently.

frankbraker, 2023-09-17:
Now even after I remove the 10uF cap from reset it doesn't program:
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

Now if I revert to the old stuff that worked before for me, and I select the atmega328new_A988driver - it builds and does upload successfully - so there's something that has broken in the latest branch.  When I try to build that it gives an error "no id" or something like that.

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

AND THEN, for no explainable reason, trying it again on your latest commit on your branch and it suddenly does upload!  No idea why, when it failed at least 4 times before.

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

I'll try this now to see how much better it works (if at all).

frankbraker, 2023-09-17:
Yes it connects and sort of works.  It is way too slow, and I imagine it might be best to at least half, if not quarter step to insure steps are never ever missed, but the problem that opened this bug seems to be addressed now and I'm able to send commands over NINA.  Thanks for the help!

frankbraker, 2023-09-17:
Unless anybody wants to reopen this I'm marking it closed.

Closed 2023-09-17.

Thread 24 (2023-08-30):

28BYJ-48 stepper motor idle issue

asahiGR, 2023-08-30:
Hello,

when there is no action and the motor is idle, it continuously clicks and get fairly warm after a while. The led on the driver pcb rotate showing it's active but not moving. Any way to stop it if there's no input? Some addition to the code?

fehlfarbe, 2023-08-31:
Hi!

As you mentioned before, the motor driver is turned off if there was no movement for 15s (millisDisableDelay) and there shouldn't be a difference if the focuser is connected to a PC, a power bank or 5V power supply.

If the driver LEDs are blinking the controller sends movement signal to the driver or a loose connection or some similar hardware problem creates signals? Did you connect the GND from the driver board to the GND of the nano? I just tried with my 28BYJ-48 setup and the LEDs turn off after the 15s delay - even when working with a power bank.

asahiGR, 2023-09-04:
Hi, thanks for you feedback. The motor works good, i've installed buttons and work it in two speeds. Everything runs smooth. Only problem, it does not turn off. All wiring is correct, gnd and power supply is common with arduino power supply. I flashed it again with nanoatmega328  config, same issue. I am using arduino nano clone CH340 in case it matters.

nettylink, 2024-01-22:
Hi,
I've seen the same behavoir, when using the buttons and the potentiometer is completly open / at "full speed".
After decrasing the speed with the potentiometer a tiny bit I've not seen this issue anymore.

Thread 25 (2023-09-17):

Changes to Readme to explain where to change time/step, step resolution, etc.

frankbraker, 2023-09-17:
So things look really great right now - in that they seem like they are within reach.

I am sort of confident that I could try to manually change the time/step and the step resolution and get my hardware to work with the moonlite focuser I have.

However, I'd really like to follow the directions on the tin, and right now there isn't a lot of detail in this domain.

When I just build what is at the top of the latest branch, and run it, I believe I had hard-wired my driver to use 1/2 steps, or maybe 1/4 steps.  So that might be a problem for starters.

If I change nothing, I find that the Moonlite ASCOM driver limits how many steps can be traversed by 10,000.  But if I try to move 10,000 steps, it doesn't move very far - less than a millimeter.  This means I probably got a wire lose to the coils, or backwards.  But it's strange because I can use the buttons and they seem to work - or at least they did work fine at one point.  Regardless of all this, it would be really nice to have it pointed out in the README file where to look in the code for fine tuning the firmware to match the configuration of hardware in use.

fehlfarbe, 2023-09-19:
Hi!
Sorry, I had too much work to do the last days. Maybe I will find some time this week to add some more tips for beginners to the readme and move some default values to macros. If you leave the MSx pins unconnected on the driver it should already work in full step configuration:

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
(I will add a link to the [Polulu doc](https://www.pololu.com/product/1182))

At least I finished my focuser dev board so I don't have to fiddle around with loose breadboard connections anymore :smiley:
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

I'm also planning to implement the arduino web uploader ( https://github.com/dbuezas/arduino-web-uploader ) for this project so beginners don't have to install platformio and can flash their Arduino via browser.

frankbraker, 2023-09-24:
Those are okay, and thanks for trying to answer my question.

What I was really asking for are the variables in the code that could be better documented.  Right now I'm just guessing at what is okay to change and what I would be better off leaving alone.

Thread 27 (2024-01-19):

Cnc shield arduino nano

hpacone, 2024-01-19:
Hallo, erstmal erstmal ein großes Lob an dich und dein Projekt!!
Dann eine riesen bitte! Glaubst du wäre es dir möglich das ganze auf einen Arduino Uno umzusetzen?? Best greetings from Austria ✌️

fehlfarbe, 2024-01-20:
Hi,

you can also write in German if that's easier for you :)

I added a version for Arduino Uno and CNC shield in the [arduino_uno_cnc_shield](https://github.com/fehlfarbe/arduino-motorfocus/tree/arduino_uno_cnc_shield) branch. Just checkout the new branch and try to flash your Uno with this version. I'm controlling the X axis motor. Unfortunately I don't have a CNC shield at home so I cannot test the changes. If it doesn't work, I will order a shield from eBay to test the code.

hpacone, 2024-01-21:
Hallo,
das ist wirklich sehr nett von dir ich danke dir vielmals!!! Ich werde das die Tage testen und dir ein Feedback geben! Dankeschön
Glg

fehlfarbe, 2024-01-23:
Hey, ich habe gerade noch mal ein paar Anpassungen vorgenommen. Leider wurden meine Pinänderungen im Code wieder überschrieben. Da mein CNC-Shield vorhin ankam, konnte ich es auch gleich testen. Bei meinem Motorkabel sind vermutlich die Pins vertauscht, daher springt er gerade nur hin und her. Ich hoffe, bei dir klappt das.

Die Buttons zum rein/raus zoomen sind auf die Z/Y Endstops gelegt. Damit kannst du es auch probieren.

hpacone, 2024-01-23:
Danke für deine Bemühungen! Ich werde das morgen gleich probieren. ✌️

hpacone, 2024-02-02:
HI, leider finde ich keine Eintrag zu flashen eines Unos in der Auswahlliste!?
Ich finde auch bei den env keinen Eintrag zum uno cnc shield.
Danke Sg

fehlfarbe, 2024-02-02:
Hast du den richtigen git branch ausgecheckt?

```
git pull
git checkout arduino_uno_cnc_shield
```

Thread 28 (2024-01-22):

DS18B20 temperature sensor no "negative values"

nettylink, 2024-01-22:
Hi,

I'm using the arduino-motorfocus with N.I.N.A. and have noticed, that negative temperatures are not shown correctly.
With negative temperatures always 0.00° are shown.

The current code always returns "0#" on negative temperature readings of the DS18B20.

I've change the following code from:
```
    byte t_int = (byte)temperature << 1;
    t_int += round(temperature - (byte)temperature);
    Serial.print(t_int, HEX);
    Serial.print('#');
```
to:
```
    int t_int = (int) temperature;
    int tmp = (t_int * 2);
    char tempString[8];
    sprintf(tempString, "%04X", (int) tmp);
    Serial.print(tempString);
    Serial.print('#');
```
I guess there are better solutions, but with this code negative temperatures are shown correctly.

fehlfarbe, 2024-01-24:
Thanks! I tested several values and simplified the code a bit :)

nettylink, 2024-01-30:
Hi,

thank you very much for the new code.
I've also tested a bit more.

When duplicating the temperature as integer, we get a 1 degree resulution.
```
int16_t t_int = (int16_t)(temperature*2);
```

When duplicating the temperature as a float, we get a 0.5 degree temp resulution.
```
float d_temperature = (float)(temperature*2);
int16_t t_int = (int16_t)(d_temperature);
```
Here are few test values.
| temperature (from DS18B20) | tempString (old) | tempString (old as int) | in N.I.N.A. (old) | tempString (new) | tempString (new as int) | in N.I.N.A. (new) |
| --- | --- | --- | --- | --- | --- |  --- |
| 4.49   | 0008     | 8   | 4.00   | 0008     | 8   | 4.00 |
| 4.51   | 0008     | 8   | 4.00   | 0009     | 9   | 4.50 |
| \-4.49 | FFFFFFF8 | \-8 | \-4.00 | FFFFFFF8 | \-8 | \-4.00 |
| \-4.51 | FFFFFFF8 | \-8 | \-4.00 | FFFFFFF7 | \-9 | \-4.50 |

fehlfarbe, 2024-02-01:
Ok that's weird because the temperature is duplicated as float in the parenthesis and afterwards casted to integer so it should be the same :thinking:

```
(int16_t)(temperature*2) == (int16_t)((float)(temperature*2))
```

Closed 2024-01-24.

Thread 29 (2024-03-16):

strange problem

SpaceRak, 2024-03-16:
I have an interesting problem with this project.  when I test pins d7-d8 to gnd, the motor rotates in both directions.  but when I try to do it with ascom or nina, the motor only rotates clockwise

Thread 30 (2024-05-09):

How do I Install Minicore Bootloader?

NovaAstrophotos, 2024-05-09:
I don't have any knowledge about programming or Arduino, but I liked your project and decided to make a auto focuser for my telescope, I managed to insert your code through Arduino, but the Moonlite didn't recognize it, so I would like to know how to insert the minicore bootloader into your code.

I'm using the cheap Arduino Nano clone called:

Nano 3.0 with the bootloader for arduino CH340 USB driver 16Mhz ATMEGA328P and a ULN2003 board with 28BYJ-48 5V 4-Phase Stepper from aliexpress.

I would like to know if you could make a mini tutorial teaching how to inject the Mini Core bootloader into your project, or recommend a tutorial so I can learn more.

fehlfarbe, 2024-05-09:
Hi,
I assume you are using Windows? Sometimes flashing the Mini Core bootloader isn't enough. I would suggest just to install a 10µF or 33µF capacitor between RST and GND. This prevents the Nano from reboot when the COM port is opened.

NovaAstrophotos, 2024-05-09:
Hi, I managed to install the minicore bootloader, but even so Moonlite I couldn't find it, I'm going to buy some capacitors, which is the correct side that I have to install the capacitor on?, my Arduino has RST and GND on both sides. thanks in advance

fehlfarbe, 2024-05-14:
The side shouldn't matter. Afaik both pins are connected to the same pin on the microcontroller.

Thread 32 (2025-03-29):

The capacitor trick has an issue

pulsar123, 2025-03-29:
First of all, thanks for this project!

I have an issue with the capacitor trick - my ASCOM driver couldn't connect to the focuser until I soldered 10 uF capacitor between RST and GND of Arduino Nano. Now it connects all right, but I have another issue - I can no longer reprogram Arduino. (Arduino IDE fails to connect.) Is it a known issue? May be changing the value of the add-on capacitor can help? Or the only solution is to solder/desolder the capacitor every time I need to reprogram the board?

I also have a question about the meaning of the speed parameters: speedFactor and speedFactorRaw. In your code the values for these two are 16 and 4. Do I need to keep these values, and only change SPEED_MULTIPLICATOR  to achieve the speed I need? In my case, I am using 1/32 microsteps, and my target speed and acceleration are 3765 ustep/s and 941 ustep/s^2, respectively.

Finally, I do not use IN/OUT buttons or a pot. I just set

int btn_in = HIGH;
int btn_out = HIGH;

throughout the code - this should do the trick, correct?

MonsieurFantome, 2025-04-14:
You can program by hitting the reset button at the right time but it's tricky.

fehlfarbe, 2025-04-15:
Hey @pulsar123, sorry for my late replay!

As @MonsieurFantome suggested, you can try to press the button at the right time or maybe solder a switch/button in between like `RST -> 10µF cap -> switch -> GND` so you can use the switch to select "programming mode" or "ASCOM mode".

I think changing the `SPEED_MULTIPLICATOR` to a higher value should  do the job because the `speedFactor`, which is set via ASCOM, is multiplied with this value.

You can set the buttons manually to `HIGH` but this shouldn't be necessary because Arduino's internal pullups are already set to `HIGH`:
```
// setup buttons
pinMode(BTN_IN, INPUT_PULLUP);
pinMode(BTN_OUT, INPUT_PULLUP);
pinMode(BTN_POTI_SPEED, INPUT_PULLUP);
```

pulsar123, 2025-04-15:
Thanks for all replies, I ended up soldering a tiny switch.

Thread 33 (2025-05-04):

Arduino motor focus gets stuck after releasing either the BTN_IN or BTN_OUT button

nettylink, 2025-05-04:
Hello,
I've noticed an occasional issue where the Arduino motor focus gets stuck after releasing either the BTN_IN or BTN_OUT button.
The motor continues to rotate slowly, and I lose control via the buttons and have to reboot the arduino.

After examining the code, I believe I've identified a potential bug:
The system sometimes gets stuck in arduino-motorfocus.cpp line 417-420 after releasing a button.
This seems to occur when the intHandler function moves the motor between lines 416 and 417.
At this point, isInManualMode is still true.
Consequently, intHandler continues to execute stepper.runSpeed(), and stepper.distanceToGo() keeps increasing.
The stepper.moveTo(stepper.currentPosition()) command, which is intended to stop the motor at the current position, isn't executed because that requires stepper.run() to be called.

Proposed Solution:
To fix this, I suggest moving the line isInManualMode = false; from line 428 to before line 415."

```
415    // // stop and ensure the stepper isn't moving anymore
416    stepper.moveTo(stepper.currentPosition());
417    while (stepper.distanceToGo())
418    {
419      debugSerial.println("Stopping motor...");
420    }
421
422    // reset speed
423    stepper.setMaxSpeed(tmpMaxSpeed);
424    stepper.setSpeed(tmpSpeed);
425
426    millisLastMove = millis();
427    currentPosition = targetPosition = stepper.currentPosition();
428    isInManualMode = false;
```

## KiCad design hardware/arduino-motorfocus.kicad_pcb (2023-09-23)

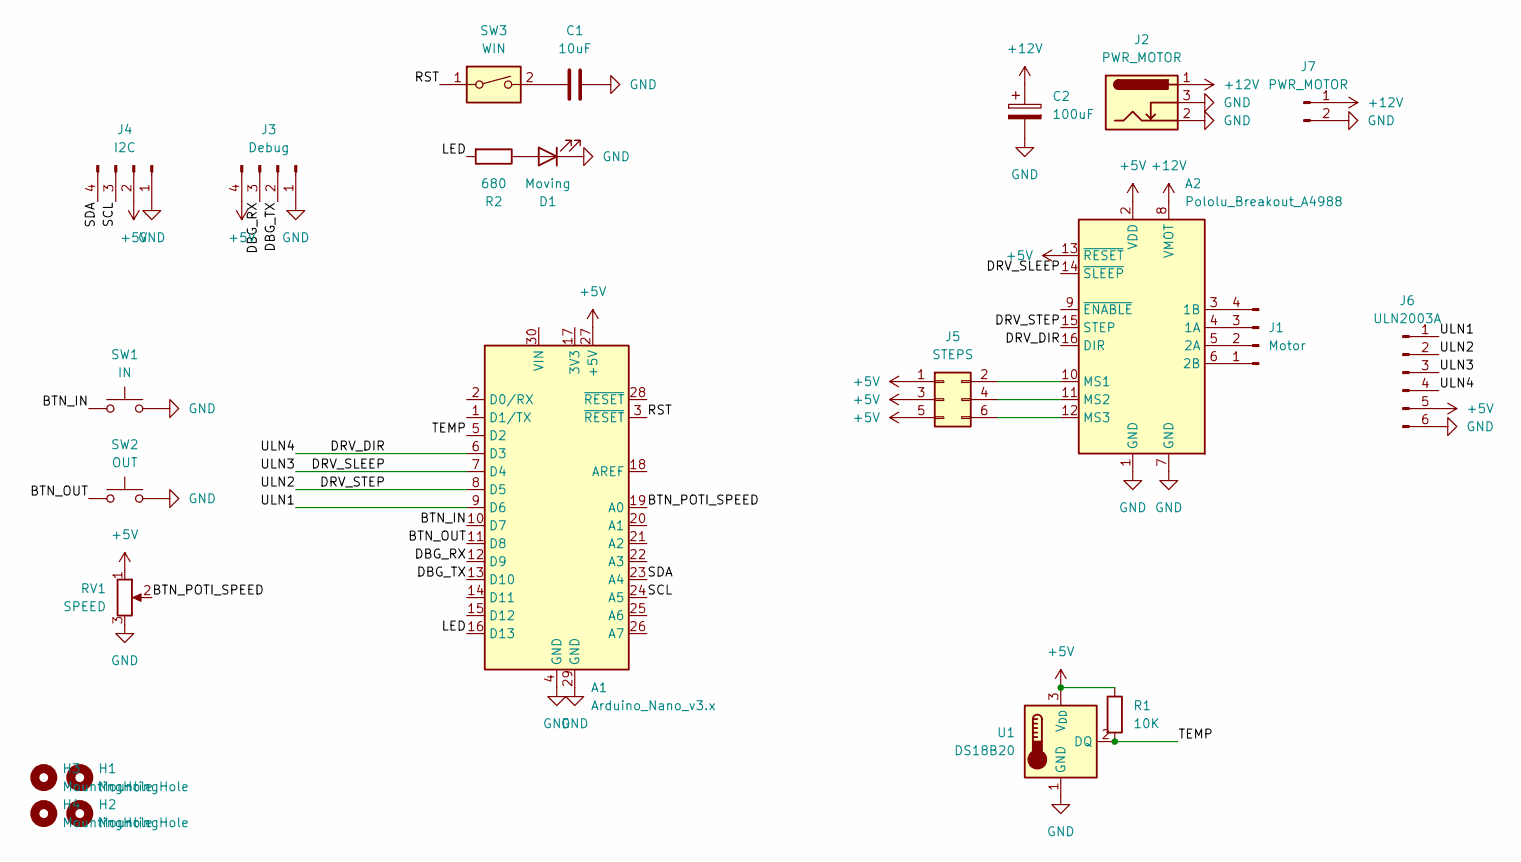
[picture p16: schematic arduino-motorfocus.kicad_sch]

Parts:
A1: Arduino_Nano_v3.x; Arduino_Nano
A2: Pololu_Breakout_A4988; Pololu_Breakout-16_15.2x20.3mm
C1: 10uF; C_1206_3216Metric
C2: 100uF; CP_Elec_6.3x5.9
D1: Moving; LED_0805_2012Metric
H1, H2, H3, H4: MountingHole; MountingHole_3.2mm_M3
J1: Motor; JST_XH_B4B-XH-A_1x04_P2.50mm_Vertical
J2: PWR_MOTOR; BarrelJack_Horizontal
J3: Debug; PinHeader_1x04_P2.54mm_Vertical
J4: I2C; PinHeader_1x04_P2.54mm_Vertical
J5: STEPS; PinHeader_2x03_P2.54mm_Vertical
J6: ULN2003A; PinHeader_1x06_P2.54mm_Vertical
J7: PWR_MOTOR; PinHeader_1x02_P2.54mm_Vertical
R1: 10K; R_1206_3216Metric
R2: 680; R_1206_3216Metric
RV1: SPEED; Potentiometer_Vishay_T73YP_Vertical
SW1: IN; SW_SPST_CK_RS282G05A3
SW2: OUT; SW_SPST_CK_RS282G05A3
SW3: WIN; SW_DIP_SPSTx01_Slide_6.7x4.1mm_W6.73mm_P2.54mm_LowProfile_J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
U1: DS18B20; TO-92_Inline

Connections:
+5V: A1.27 (+5V), A2.2 (VDD), A2.13 (~RESET), J3.4, J4.2, J5.1, J5.3, J5.5, J6.5, R1.1, RV1.1, U1.3 (V_{DD})
+12V: A2.8 (VMOT), C2.1, J2.1, J7.1
/BTN_IN: A1.10 (D7), SW1.1
/BTN_OUT: A1.11 (D8), SW2.1
/BTN_POTI_SPEED: A1.19 (A0), RV1.2
/DBG_RX: A1.12 (D9), J3.3
/DBG_TX: A1.13 (D10), J3.2
/DRV_DIR: A1.6 (D3), A2.16 (DIR), J6.4
/DRV_SLEEP: A1.7 (D4), A2.14 (~SLEEP), J6.3
/DRV_STEP: A1.8 (D5), A2.15 (STEP), J6.2
/LED: A1.16 (D13), R2.2
/RST: A1.3 (~RESET), SW3.1
/SCL: A1.24 (A5), J4.3
/SDA: A1.23 (A4), J4.4
/TEMP: A1.5 (D2), R1.2, U1.2 (DQ)
/ULN1: A1.9 (D6), J6.1
GND: A1.4 (GND), A1.29 (GND), A2.1 (GND), A2.7 (GND), C1.2, C2.2, D1.1 (K), J2.2, J2.3, J3.1, J4.1, J6.6, J7.2, RV1.3, SW1.2, SW2.2, U1.1 (GND)
unnamed: A2.4 (1A), J1.3
unnamed: A2.3 (1B), J1.4
unnamed: A2.5 (2A), J1.2
unnamed: A2.6 (2B), J1.1
unnamed: A2.10 (MS1), J5.2
unnamed: A2.11 (MS2), J5.4
unnamed: A2.12 (MS3), J5.6
unnamed: C1.1, SW3.2
unnamed: D1.2 (A), R2.1

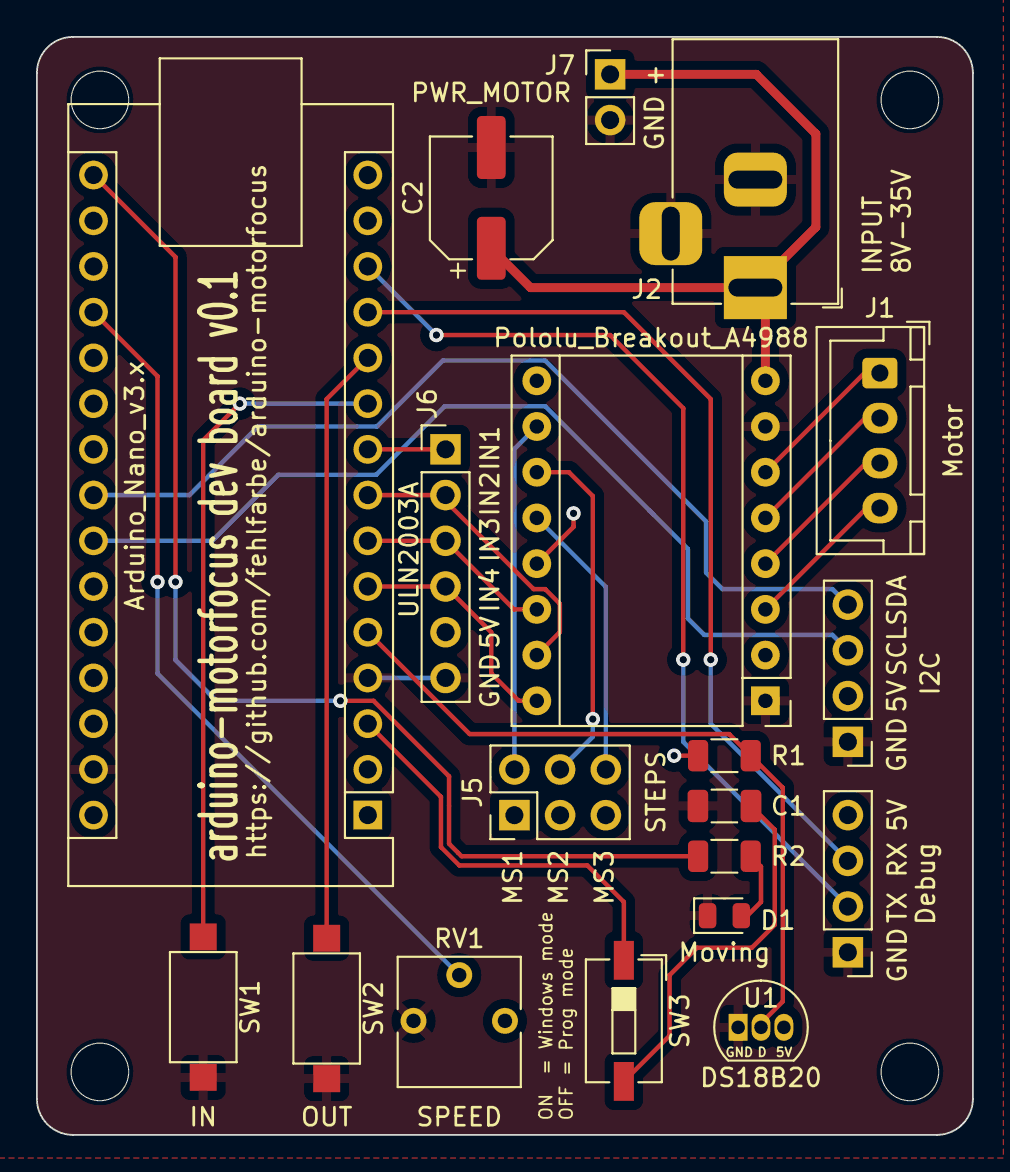
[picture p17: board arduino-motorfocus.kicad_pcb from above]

Board: 2 copper layers, 52.0 x 61.0 mm, 23 parts (0 on the bottom side), 26 nets.

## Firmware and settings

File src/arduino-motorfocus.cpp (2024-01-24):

#include <Arduino.h>
#include <SoftwareSerial.h>
#include <AccelStepper.h>
#include <EEPROM.h>
#include <OneWire.h>
#include <DallasTemperature.h>
#include <TimerOne.h>
#include "DummySerial.h"

#define BTN_IN 7
#define BTN_OUT 8
#define BTN_POTI_SPEED A0
#define BTN_MIN_SPEED 8
#define BTN_MAX_SPEED 512
#define BTN_ACCEL_FACTOR 1.05f

#define PIN_DRIVER_SLEEP 4
#define PIN_DRIVER_DIR 3
#define PIN_DRIVER_STEP 5

#define ONE_WIRE_BUS 2

#define PERIOD_US 2000

// Maximum motor speed multiplicator in steps per second
#define SPEED_MULTIPLICATOR 30
// Motor acceleration in steps per second per second
#define ACCELERATION 100

// #define USE_DRIVER

// #define DEBUG
#ifdef DEBUG
SoftwareSerial debugSerial(9, 10);
#else
DummySerial debugSerial;
#endif

// initialize the stepper library
#ifdef USE_DRIVER
AccelStepper stepper(AccelStepper::DRIVER, PIN_DRIVER_STEP, PIN_DRIVER_DIR);
#else
AccelStepper stepper(AccelStepper::FULL4WIRE, 6, 4, 5, 3, false);
#endif

// temperature
OneWire oneWire(ONE_WIRE_BUS);
DallasTemperature sensors(&oneWire);

// multiplier of SPEEDMUX, currently max speed is 480.
int speedFactor = 16;
int speedFactorRaw = 4;

float tCoeff = 0;

// button
unsigned long currentPosition = 0;
unsigned long targetPosition = 0;
unsigned long lastSavedPosition = 0;
long millisLastMove = 0;
const long millisDisableDelay = 15000;
bool isEnabled = false;
bool isInManualMode = false;

// read commands
bool eoc = false;
String line;

// function declarations
long hexstr2long(String line);
static void intHandler();
int readButtonSpeed();

/*************************************
 * SETUP
 *************************************/
void setup()
{
  Serial.begin(9600);
  debugSerial.begin(9600);

  // setup pins
  pinMode(LED_BUILTIN, OUTPUT);
  digitalWrite(LED_BUILTIN, LOW);

  // initalize motor
  debugSerial.println("init motor driver...");
  stepper.setMaxSpeed(speedFactor * SPEED_MULTIPLICATOR);
  stepper.setAcceleration(ACCELERATION);
#ifdef USE_DRIVER
  debugSerial.println("Using A4988 driver");
  stepper.setEnablePin(PIN_DRIVER_SLEEP);
  stepper.disableOutputs();
  isEnabled = false;
#endif
  millisLastMove = millis();

  // read saved position from EEPROM
  // EEPROM.put(0, (long)0);
  EEPROM.get(0, currentPosition);
  // prevent negative values if EEPROM is empty
  currentPosition = max(0, currentPosition);

  stepper.setCurrentPosition(currentPosition);
  lastSavedPosition = currentPosition;
  targetPosition = currentPosition;
  debugSerial.print("Last position in EEPROM...");
  debugSerial.println(lastSavedPosition);

  // init temperature sensor
  sensors.begin();
  if(sensors.getDeviceCount()){
    debugSerial.println("Found DS18B20 temperature sensor!");
  }

  // setup buttons
  pinMode(BTN_IN, INPUT_PULLUP);
  pinMode(BTN_OUT, INPUT_PULLUP);
  pinMode(BTN_POTI_SPEED, INPUT_PULLUP);

  // init timer
  Timer1.initialize(PERIOD_US);
  Timer1.attachInterrupt(intHandler);
}

/*************************************
 * LOOP
 *************************************/
void loop()
{

  // process the command we got
  if (eoc)
  {
    debugSerial.print("Got new command: ");
    debugSerial.println(line);

    if (line.startsWith("2"))
    {
      debugSerial.println("Got Dual focuser command(?) starting with 2. Send values of first motor");
      // remove first character and parse command
      line = line.substring(1);
    }

    String cmd, param;
    int len = line.length();
    if (len >= 2)
    {
      cmd = line.substring(0, 2);
    }
    else
    {
      cmd = line.substring(0, 1);
    }
    if (len > 2)
    {
      param = line.substring(2);
    }

    debugSerial.print("Got line: ");
    debugSerial.println(line);
    debugSerial.print("Command: ");
    debugSerial.print(cmd);
    if (param.length())
    {
      debugSerial.print(" Param: ");
      debugSerial.print(param);
    }
    debugSerial.println();

    line = "";
    eoc = false;

    // LED backlight value, always return "00"
    if (cmd.equalsIgnoreCase("GB"))
    {
      Serial.print("00#");
    }
    // home the motor, hard-coded, ignore parameters since we only have one motor
    if (cmd.equalsIgnoreCase("PH"))
    {
      stepper.setCurrentPosition(8000);
      stepper.moveTo(0);
    }
    // firmware value, always return "10"
    if (cmd.equalsIgnoreCase("GV"))
    {
      Serial.print("10#");
    }
    // Initiate a temperature conversion the conversion
    // process takes a maximum of 750 milliseconds. The
    // value returned by the :GT# command will not be
    // valid until the conversion process completes.
    if (cmd.equalsIgnoreCase("C"))
    {
      debugSerial.println("No temperature conversion implemented, yet");
      // Serial.print("10#");
    }
    // get the current motor position
    if (cmd.equalsIgnoreCase("GP"))
    {
      currentPosition = stepper.currentPosition();
      char tempString[6];
      sprintf(tempString, "%04lX", currentPosition);
      Serial.print(tempString);
      Serial.print("#");

      debugSerial.print("current motor position: 0x");
      debugSerial.print(tempString);
      debugSerial.print(" = ");
      debugSerial.println(currentPosition);
    }
    // get the new motor position (target)
    if (cmd.equalsIgnoreCase("GN"))
    {
      // pos = stepper.targetPosition();
      char tempString[6];
      sprintf(tempString, "%04lX", targetPosition);
      Serial.print(tempString);
      Serial.print("#");

      debugSerial.print("target motor position: ");
      debugSerial.println(tempString);
    }
    // get the current temperature from DS1820 temperature sensor
    if (cmd.equalsIgnoreCase("GT"))
    {
      sensors.requestTemperatures();
      float temperature = sensors.getTempCByIndex(0);
      debugSerial.print("temperature: ");
      debugSerial.println(temperature);
      if (temperature > 100 || temperature < -50)
      {
        // error
        temperature = 0;
      }
      debugSerial.print("Current temperature ");
      debugSerial.println(temperature);
      // convert to 16bit hex number
      // INDI reads temp via static_cast<int16_t>(temp) / 2.0;
      // so multiply temperature by 2 and cast to int16
      int16_t t_int = (int16_t)(temperature*2);
      char tempString[5];
      sprintf(tempString, "%04X", (int16_t)t_int);
      Serial.print(tempString);
      Serial.print('#');
    }

    // get the temperature coefficient
    if (cmd.equalsIgnoreCase("GC"))
    {
      // Serial.print("02#");
      Serial.print((byte)tCoeff, HEX);
      Serial.print('#');
    }

    // set the temperature coefficient
    if (cmd.equalsIgnoreCase("SC"))
    {
      // debugSerial.println(param);
      if (param.length() > 4)
      {
        param = param.substring(param.length() - 4);
      }
      debugSerial.println(param);

      if (param.startsWith("F"))
      {
        // debugSerial.println("negative");
        // debugSerial.println(strtol("FFFF", NULL, 16));
        // debugSerial.println(strtol(param.c_str(), NULL, 16));
        tCoeff = ((0xFFFF - strtol(param.c_str(), NULL, 16)) / -2.0f) - 0.5f;
      }
      else
      {
        tCoeff = strtol(param.c_str(), NULL, 16) / 2.0f;
      }
      debugSerial.print("t_coeff: ");
      debugSerial.println(tCoeff);
      // Serial.print("02#");
    }

    // get the current motor speed, only values of 02, 04, 08, 10, 20
    if (cmd.equalsIgnoreCase("GD"))
    {
      char tempString[6];
      sprintf(tempString, "%02X", speedFactorRaw);
      Serial.print(tempString);
      Serial.print("#");

      debugSerial.print("current motor speed: ");
      debugSerial.println(tempString);
    }

    // set speed, only acceptable values are 02, 04, 08, 10, 20
    if (cmd.equalsIgnoreCase("SD"))
    {
      speedFactorRaw = hexstr2long(param);

      // SpeedFactor: smaller value means faster
      speedFactor = 32 / speedFactorRaw;
      stepper.setMaxSpeed(speedFactor * SPEED_MULTIPLICATOR);
    }

    // whether half-step is enabled or not, always return "00"
    if (cmd.equalsIgnoreCase("GH"))
    {
      Serial.print("00#");
    }

    // motor is moving - 01 if moving, 00 otherwise
    if (cmd.equalsIgnoreCase("GI"))
    {
      if (stepper.distanceToGo() != 0)
      {
        Serial.print("01#");
        debugSerial.print("Motor is moving, target = ");
        debugSerial.print(targetPosition);
        debugSerial.print(" current = ");
        debugSerial.println(currentPosition);
      }
      else
      {
        Serial.print("00#");
        debugSerial.println("Motor is not moving");
      }
    }
    // set current motor position
    if (cmd.equalsIgnoreCase("SP"))
    {
      currentPosition = hexstr2long(param);
      stepper.setCurrentPosition(currentPosition);
    }
    // set new motor position
    if (cmd.equalsIgnoreCase("SN"))
    {
      // Serial.println(param);
      debugSerial.print("new target position ");
      debugSerial.print(targetPosition);
      debugSerial.print(" -> ");
      targetPosition = hexstr2long(param);
      debugSerial.println(targetPosition);
      // Serial.println(targetPosition);
      // stepper.moveTo(pos);
    }
    // initiate a move
    if (cmd.equalsIgnoreCase("FG"))
    {
      stepper.enableOutputs();
      isEnabled = true;
      stepper.moveTo(targetPosition);
    }
    // stop a move
    if (cmd.equalsIgnoreCase("FQ"))
    {
      stepper.stop();
    }
  }

  int btn_in = digitalRead(BTN_IN);
  int btn_out = digitalRead(BTN_OUT);

  // move motor if not done
  if (stepper.distanceToGo() != 0)
  {
    debugSerial.print("Has distance to go: ");
    debugSerial.println(stepper.distanceToGo());
    millisLastMove = millis();
    currentPosition = stepper.currentPosition();
  }
  // handle manual buttons
  else if (btn_in == LOW || btn_out == LOW)
  {
    isInManualMode = true;
    // enable motor outputs if motor is idle
    if (!isEnabled)
    {
      stepper.enableOutputs();
      isEnabled = true;
    }
    // save current speed settings
    auto tmpMaxSpeed = stepper.maxSpeed();
    auto tmpSpeed = stepper.speed();
    // run loop while buttons are pressed
    float speed = BTN_MIN_SPEED;
    stepper.setSpeed(speed);
    stepper.setMaxSpeed(readButtonSpeed());
    while (btn_in == LOW || btn_out == LOW)
    {
      debugSerial.print("Speed from poti: ");
      debugSerial.println(speed);
      stepper.setMaxSpeed(readButtonSpeed());
      if (btn_in == LOW && speed < 0)
      {
        speed = BTN_MIN_SPEED;
        debugSerial.println("Button forward ");
      }
      else if (btn_out == LOW && speed > 0)
      {
        // prevent negative values
        speed = -BTN_MIN_SPEED;
        debugSerial.println("Button backward ");
      }
      speed = constrain(speed * BTN_ACCEL_FACTOR, -stepper.maxSpeed(), stepper.maxSpeed());
      debugSerial.print("Set speed to ");
      debugSerial.println(speed);
      stepper.setSpeed(speed); // set speed with direction
      delay(25);

      // read new button values
      btn_in = digitalRead(BTN_IN);
      btn_out = digitalRead(BTN_OUT);
    }

    // // stop and ensure the stepper isn't moving anymore
    stepper.moveTo(stepper.currentPosition());
    while (stepper.distanceToGo())
    {
      debugSerial.println("Stopping motor...");
    }

    // reset speed
    stepper.setMaxSpeed(tmpMaxSpeed);
    stepper.setSpeed(tmpSpeed);

    millisLastMove = millis();
    currentPosition = targetPosition = stepper.currentPosition();
    isInManualMode = false;
  }
  else
  {
    // check if motor was'nt moved for several seconds and save position and disable motors
    if (millis() - millisLastMove > millisDisableDelay)
    {
      // Save current location in EEPROM
      if (lastSavedPosition != currentPosition)
      {
        EEPROM.put(0, currentPosition);
        lastSavedPosition = currentPosition;
        debugSerial.print("Save last position ");
        debugSerial.print(lastSavedPosition);
        debugSerial.println(" to EEPROM");
      }
      if (isEnabled)
      {
        // set motor to sleep state
        stepper.disableOutputs();
        isEnabled = false;
        debugSerial.println("Disabled output pins");
      }
    }
  }
}

// read the command until the terminating # character
void serialEvent()
{
  // read the command until the terminating # character
  while (Serial.available() && !eoc)
  {
    char c = Serial.read();
    if (c != '#' && c != ':')
    {
      line = line + c;
    }
    else
    {
      if (c == '#')
      {
        eoc = true;
      }
    }
  }
}

long hexstr2long(String line)
{
  char buf[line.length() + 1];
  line.toCharArray(buf, line.length() + 1);
  return strtol(buf, NULL, 16);
}

static void intHandler()
{
  bool moving = false;
  if (isInManualMode)
  {
    stepper.runSpeed();
    moving = abs(stepper.speed()) > 0;
  }
  else
  {
    stepper.run();
    moving = stepper.distanceToGo() != 0;
  }

  digitalWrite(LED_BUILTIN, moving);
}

int readButtonSpeed()
{
  // analogRead 0 -> min speed, 1023 -> max speed so if there is nothing connected
  // the motor will accelerate to max speed
  auto speedVal = map(analogRead(BTN_POTI_SPEED), 50, 900, BTN_MIN_SPEED, BTN_MAX_SPEED);
  return max(min(speedVal, BTN_MAX_SPEED), BTN_MIN_SPEED);
}

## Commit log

2017-10-02 disable motor pins when idle
2017-10-02 update currentPosition after stopping to correctly trigger the idle state
    [arduino-motorfocus.ino]
2018-02-23 Added input pins to control focus via button Added CMake project structure (for CLion)
2019-02-12 Added wiring Updated README.md
    [wiring.fzz]
2019-02-17 Added support for Pololu A4988 driver Changed debug serial interface pins Added input pullups Added some wiring Increased acceleration
    [wiring.fzz, wiring_buttons.fzz, wiring_driver.fzz]
2019-04-28 Set driver to default updated README
2019-04-28 revert changes, make 28BYJ-48 with driver board default again
    [arduino-motorfocus.ino]
2019-05-25 Added temperature sensor support
    [wiring_temperature.fzz]
2020-12-16 Small bugfixes and updated README
    [arduino-motorfocus.ino]
2020-12-17 Bugfix so it doesn't close connection to DualFocuser App
    [arduino-motorfocus.ino]
2021-01-03 Use of timer interrupt for the stepper.run call
    With the stepper.run() call in the arduino loop(), the motor stalls on heavy serial activity. Using a timer driven interrupt avoids that.
    [arduino-motorfocus.ino]
2021-03-17 Added Dummy Debug to prevent motor stuttering
    [arduino-motorfocus.ino]
2021-10-10 - Converted Arduino project to PlatformIO project - Minor improvements (code, doc, etc.)
    [wiring_driver.fzz]
2021-12-01 fixed iss9 DS18B20 wrong wiring
    [wiring_temperature.fzz]
2021-12-01 fixes #9 DS18B20 wrong wiring
    [wiring_temperature.fzz]
2021-12-07 fixes #10 and changed lastSavedPosition to same data type as currentPosition
    [arduino-motorfocus.cpp]
2022-08-22 Fixes #17
    [wiring_driver.fzz]
2023-02-06 Added Arduino Nano with new bootloader to platformio.ini (issue #19)
2023-02-27 Fixed wrong "moving motor" response after button press and some code improvements
    [arduino-motorfocus.cpp]
2023-08-02 Updated RST capacitor size to a higher value
2023-08-03 Added support for poti that controls the motor speed on button press
2023-08-03 Inverted poti signal so if there is nothing connected the motor will still run and minimum speed
    [arduino-motorfocus.cpp]
2023-08-05 Using timer and acceleration in button/manual mode
2023-08-29 Fixing motor running state
    [arduino-motorfocus.cpp]
2023-08-31 Created simple dev board that supports ULN2003A and A4988 driver board
    [arduino-motorfocus.kicad_pcb, arduino-motorfocus.kicad_sch]
2023-09-23 Added simple PCB project and doc
    [arduino-motorfocus.csv, arduino-motorfocus.kicad_pcb, arduino-motorfocus.kicad_sch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]
2023-09-23 Improved README (issue #25)
    [arduino-motorfocus.cpp]
2024-01-24 Fixing no negatives values for temperature sensor (issue #28)
    [arduino-motorfocus.cpp]
